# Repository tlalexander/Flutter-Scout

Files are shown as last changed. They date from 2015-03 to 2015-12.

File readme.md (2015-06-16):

# Flutter Scout printable remote control car
### Now at Version 2!

Scout is an experimental vehicle that can be printed by anyone with a 3D printer with at least 155mm of travel in one axis. The original Scout vehicles were printed on an Ultimaker, but we also recommend Printrbot, Lulzbot, and Type A Machines.

Scout does not use any screws. Sourcing screws is annoying and time consuming, and screwing things together is boring. Scout snaps together using interlocking parts and clips. The whole vehicle can be disassembled and reassembled in just a few minutes.

### Images:
http://imgur.com/a/r0YCL

### Video:
https://youtu.be/zFiCiyVp22o

### Wireless Platform
For more info on Scout's recommended wireless platform, check out http://FlutterWireless.com

### Current Issues
Scout has no crash protection for frontal crashes. Small frontal crashes can damage the steering servo horn and large direct crashes can crush the front frame member. A redesign is in the works to support a bumper and improve steering protection.
Scout V1 liked to flip over and roll back onto the wheels. Scout V2 has a flatter top and is more likely to land square upside down, requiring the operator to go flip it back over. A more turtle-like top shell should alleviate this.
Two pins in the steering system have no retaining mechanism. They will not fall out under normal operation but can fall out when Scout is upside down. This usually happens when showing someone how cool Scout's gears are.

### More details
See this blog post about Scout for some more information.
http://community.flutterwireless.com/t/introducing-flutter-scout/208

### Assembly notes

Please see the Flutter community forum for details on assembly and parts ordering for Scout.
http://community.flutterwireless.com/t/flutter-scout-robot/203

### Other notes
Flutter Scout's gears use the "Solidworks Gear Generator" file from thingiverse user msruggles, found here:
http://www.thingiverse.com/thing:8077
The developer has given me permission to use the gear files in Scout.

### License

Scout was created in early 2015 by Taylor Alexander, and is licensed under Creative Commons Attribution-ShareAlike 4.0 International (CC BY-SA 4.0), which can be viewed at: http://creativecommons.org/licenses/by-sa/4.0/

### Contact Info, press inquiries
If you would like to help with Scout or have questions for a news article, please reach out to me via email. My email is the same as my github username, but at gmail.com

### Scout V1 in the news
http://makezine.com/2015/03/12/3d-print-this-kickass-snap-together-rc-race-car/
http://blog.atmel.com/2015/03/12/scout-is-a-3d-printable-flutter-based-rc-car/

### Issues V1
These were the issues in Scout Version 1. Essentially all of them have been resolved in Version 2.

The current vehicle was designed quickly over a few weekends as a proof of concept, and so it has many flaws. A short list:
The right angle mounting of the motor creates a week point with the bevel gears.
The wheels are supposed to slip on, but using my printer they need to be hammered into place with a mallet.
The steering requires a piece of bent piano wire, and should be replaced with a printed linkage.
The body shell easily comes off, and so tape should be wrapped around the body of the system.
There is no hole in the body shell for a power switch, so without modification the tape needs to be cut to toggle power.
After agressive driving the motor gets hot and eventually wiggles in its mount.

Despite these flaws, the car is impressibly capable. It can even pull ten foot wheelies.

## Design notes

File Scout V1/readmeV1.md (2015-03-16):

# Flutter Scout printable remote control car

Scout is an experimental vehicle that can be printed by anyone with a 3D printer with at least 165mm of travel in one axis. The original Scout vehicles were printed on an Ultimaker, which is a highly recommended printer.

Scout does not use any screws. Sourcing screws is annoying and time consuming, and screwing things together is boring. Scout snaps together using interlocking parts and clips. The whole vehicle can be disassembled and reassembled in just a few minutes.

### Images:
http://imgur.com/a/Noe9S

### Video:
https://www.youtube.com/watch?v=8hfF0LrXyi8

### Scout is in the news!
http://makezine.com/2015/03/12/3d-print-this-kickass-snap-together-rc-race-car/
http://blog.atmel.com/2015/03/12/scout-is-a-3d-printable-flutter-based-rc-car/

### Wireless Platform
For more info on Scout's recommended wireless platform, check out http://www.FlutterWireless.com

### Issues

The current vehicle was designed quickly over a few weekends as a proof of concept, and so it has many flaws. A short list:
The right angle mounting of the motor creates a week point with the bevel gears.
The wheels are supposed to slip on, but using my printer they need to be hammered into place with a mallet.
The steering requires a piece of bent piano wire, and should be replaced with a printed linkage.
The body shell easily comes off, and so tape should be wrapped around the body of the system.
There is no hole in the body shell for a power switch, so without modification the tape needs to be cut to toggle power.
After agressive driving the motor gets hot and eventually wiggles in its mount.

Despite these flaws, the car is impressibly capable. It can even pull ten foot wheelies.

### Assembly notes

The wheels currently press on. If you cannot get them to fit, scale the wheel up by a few percent. If they are loose, you may want to use super glue.

The rear axle should be 100% infill for strength. Everything else can generally be 15%-30% infill (Cura calculations, other slicers may vary).

I mention using a Flutter radio to promote the product, but you can also use any normal remote control car radio, though steering may be backwards.

Any standard servo works. Other quadcopter motors should work with changes to the gear placement, but this motor is incredibly strong even with a 2s battery.

### Other notes
Flutter Scout's gears use the "Solidworks Gear Generator" file from thingiverse user msruggles, found here:
http://www.thingiverse.com/thing:8077
No license accompanies the file, but I have reached out to the developer for explicit permission. It was however shared freely on an public site so this use is assumed permitted.

### License

Scout was created in early 2015 by Taylor Alexander, and is licensed under Creative Commons Attribution-ShareAlike 4.0 International (CC BY-SA 4.0), which can be viewed at: http://creativecommons.org/licenses/by-sa/4.0/

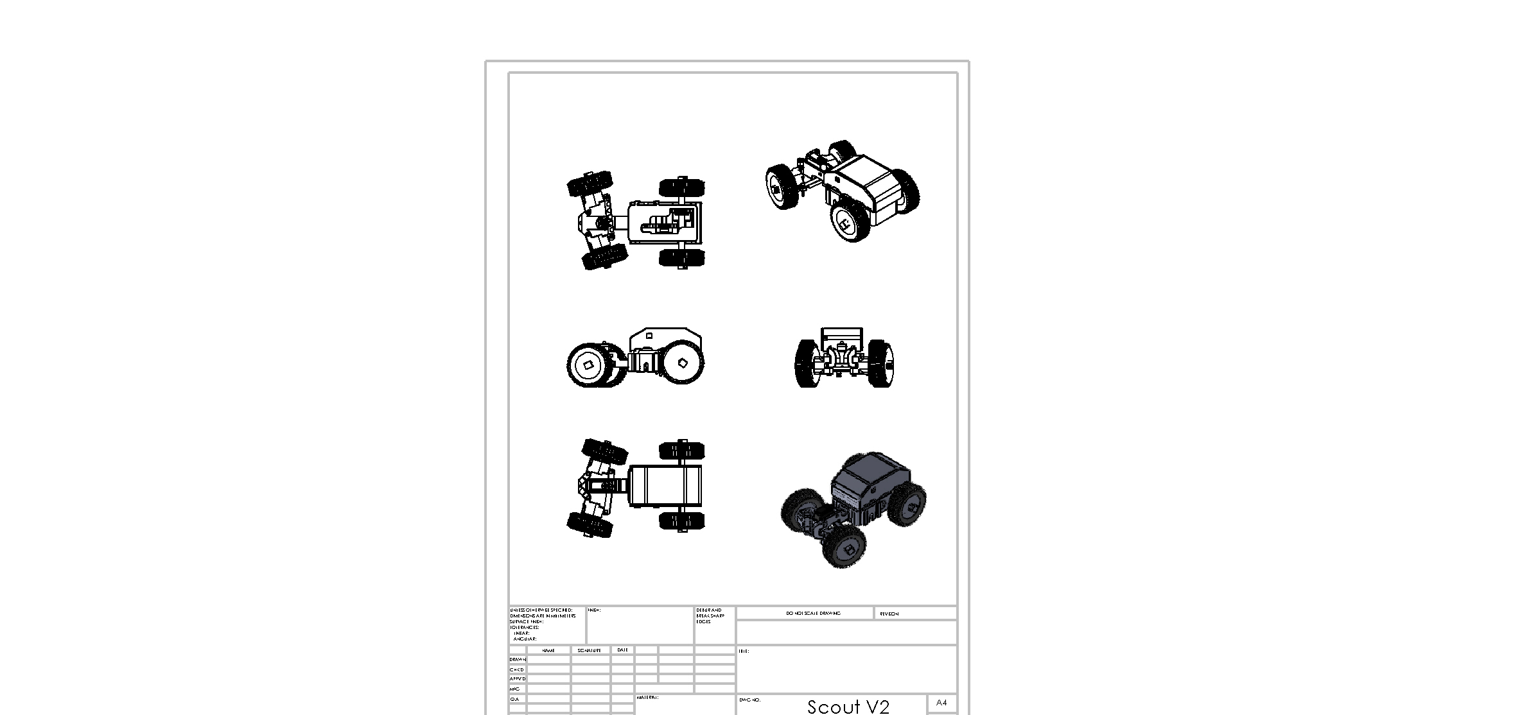
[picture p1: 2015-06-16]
Scout V2.JPG

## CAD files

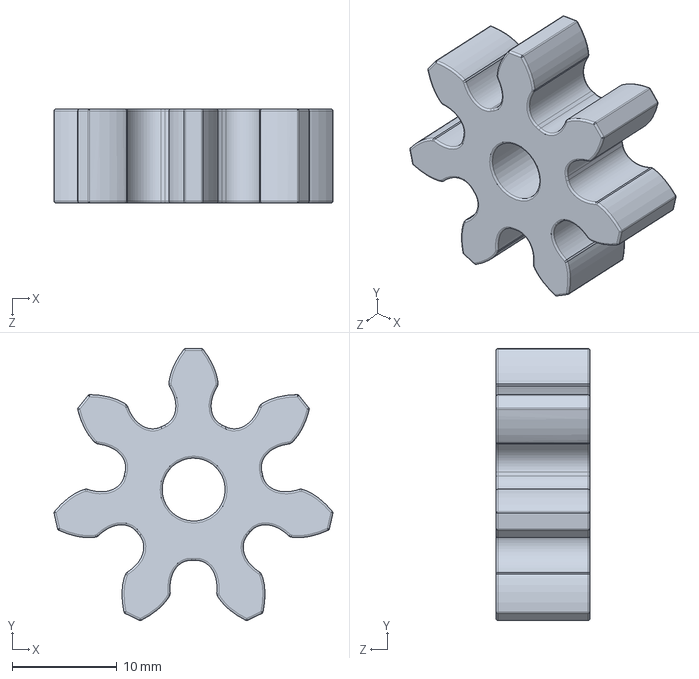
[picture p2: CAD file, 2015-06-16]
gears/main small drive gear.SLDPRT
26.6 x 26.0 x 9.00 mm

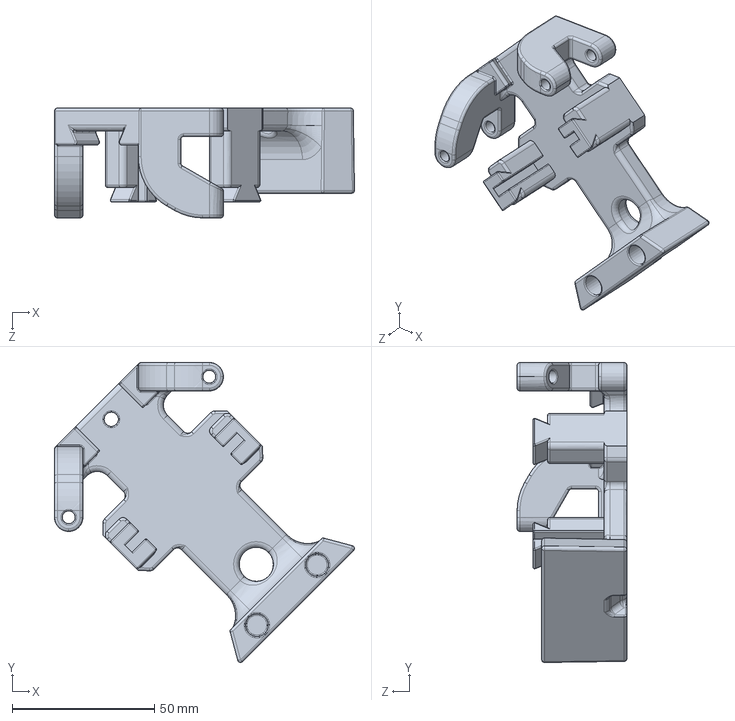
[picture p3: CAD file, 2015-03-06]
Scout V1/frame components/main frame, front.SLDPRT
105.6 x 105.6 x 38.7 mm

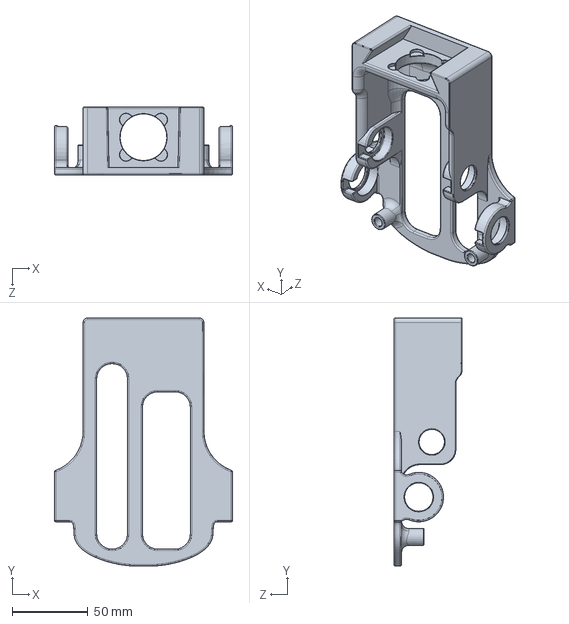
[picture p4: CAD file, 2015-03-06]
Scout V1/frame components/main frame, rear.SLDPRT
118.0 x 164.2 x 45.0 mm

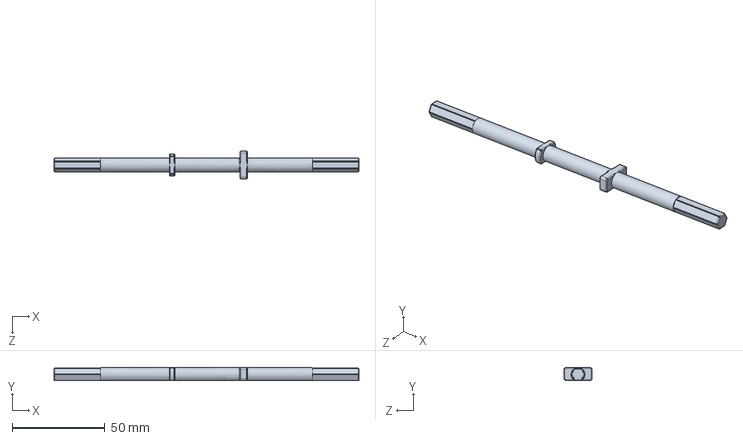
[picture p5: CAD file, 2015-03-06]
Scout V1/shafts/main axle.SLDPRT
164.0 x 7.08 x 15.0 mm

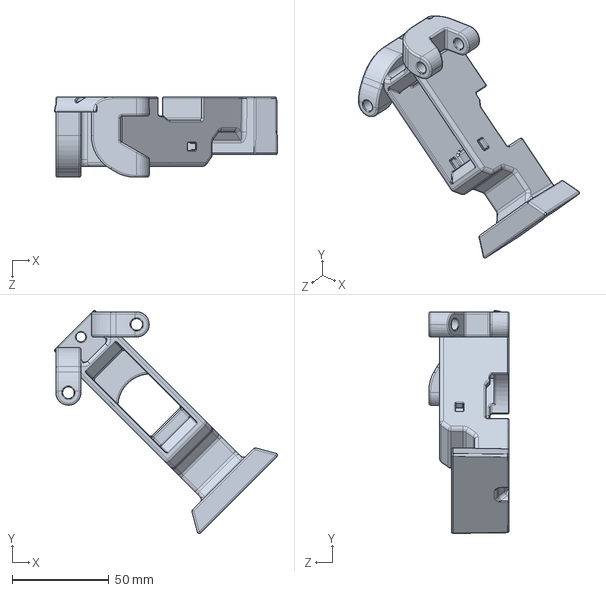
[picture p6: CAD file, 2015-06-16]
frame components/main frame, front V2.SLDPRT
115.4 x 115.4 x 41.7 mm

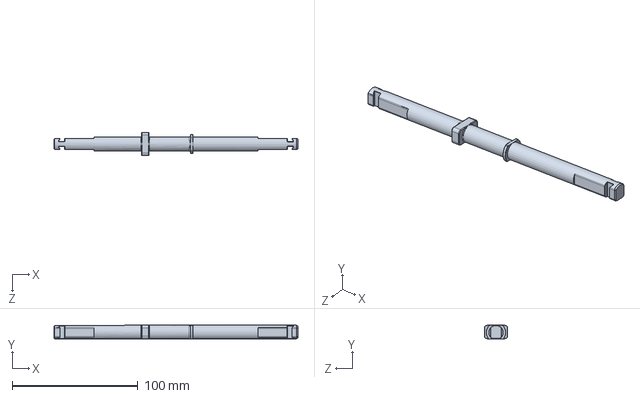
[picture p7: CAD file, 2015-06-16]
shafts/main axle 12mm.SLDPRT
194.0 x 10.8 x 18.5 mm

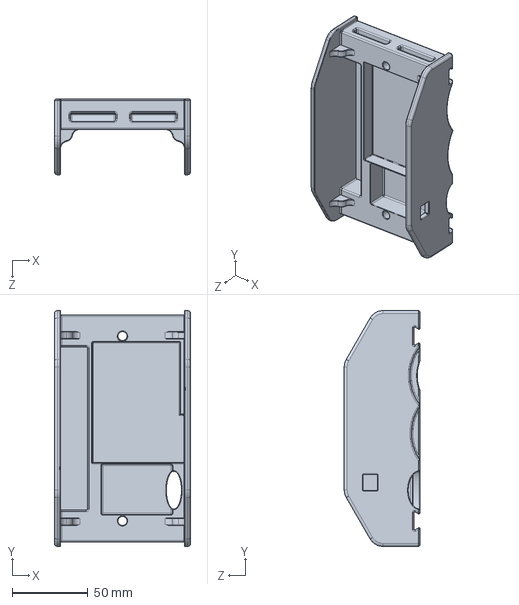
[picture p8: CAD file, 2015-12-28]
frame components/Scout tray.SLDPRT
90.0 x 156.0 x 50.0 mm

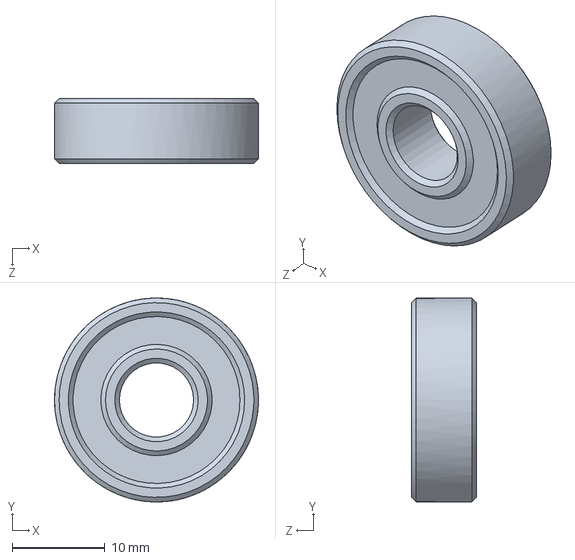
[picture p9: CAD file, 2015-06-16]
non-printed parts/608 bearing.SLDPRT
22.0 x 22.0 x 7.00 mm

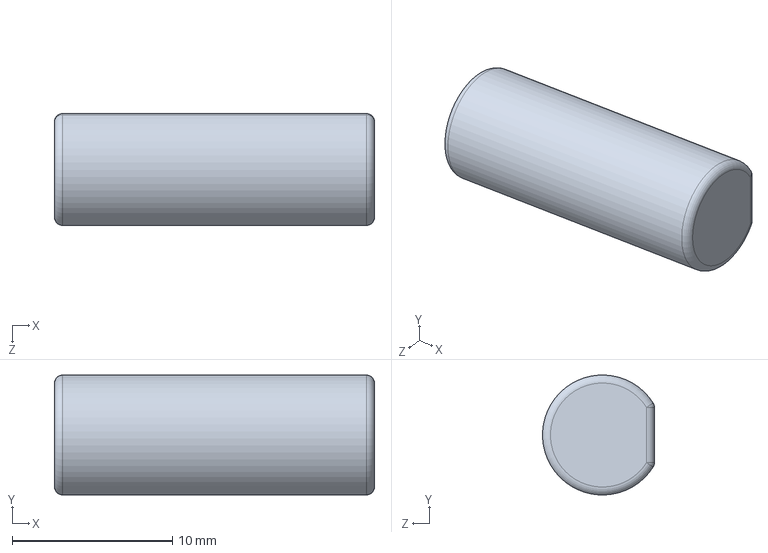
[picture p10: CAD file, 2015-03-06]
Scout V1/frame components/Body support peg front.SLDPRT
20.0 x 7.49 x 6.99 mm

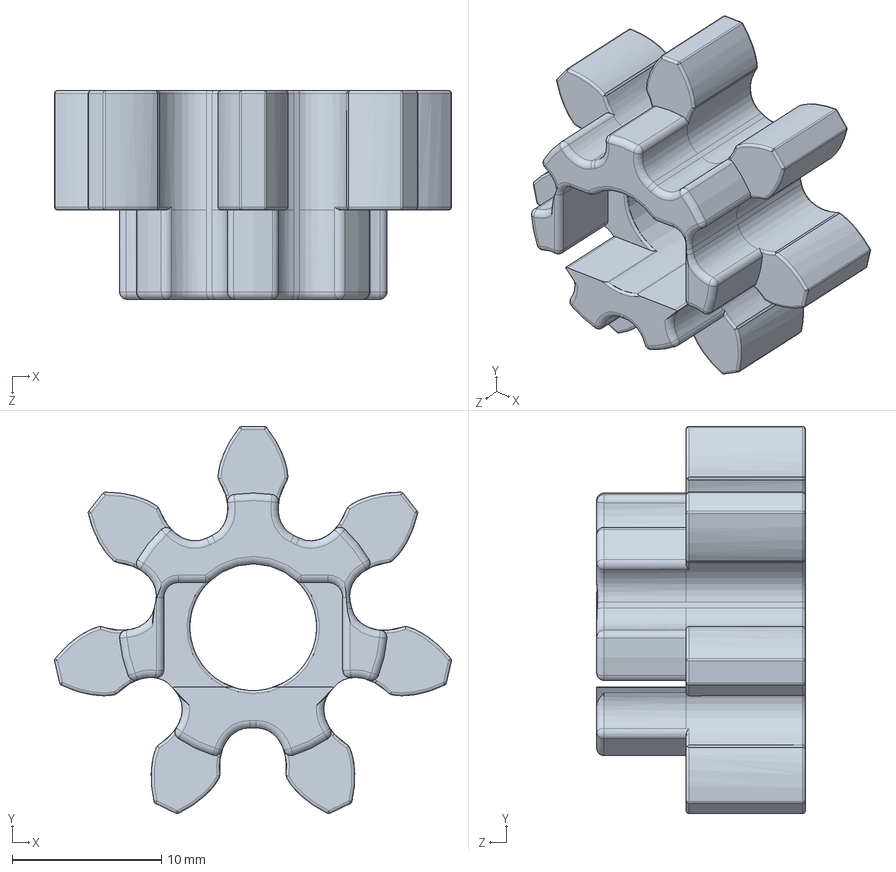
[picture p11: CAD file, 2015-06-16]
Scout V1/gears/secondary small drive gear.SLDPRT
26.6 x 26.0 x 14.0 mm

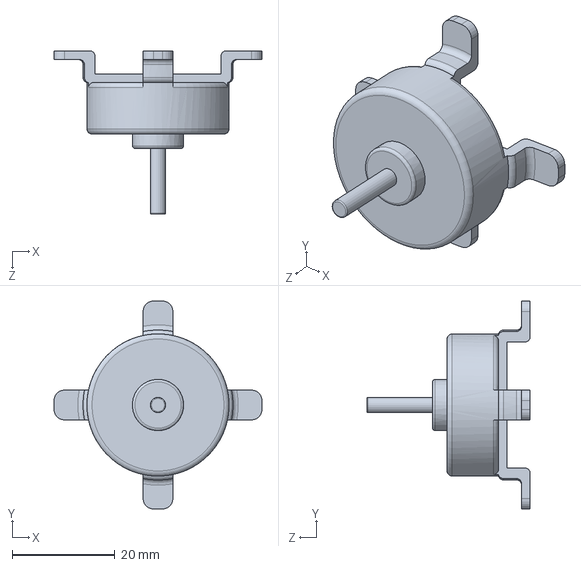
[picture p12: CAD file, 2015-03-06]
Scout V1/non-printed parts/Hobbyking Donkey ST2204.SLDPRT
40.5 x 40.5 x 31.8 mm

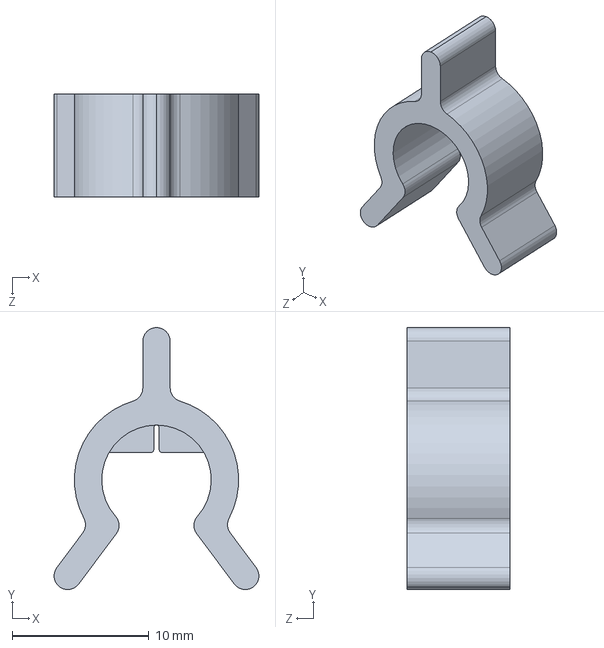
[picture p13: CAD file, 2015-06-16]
Scout V1/shafts/clip, forward drive shaft.SLDPRT
15.0 x 19.1 x 7.50 mm

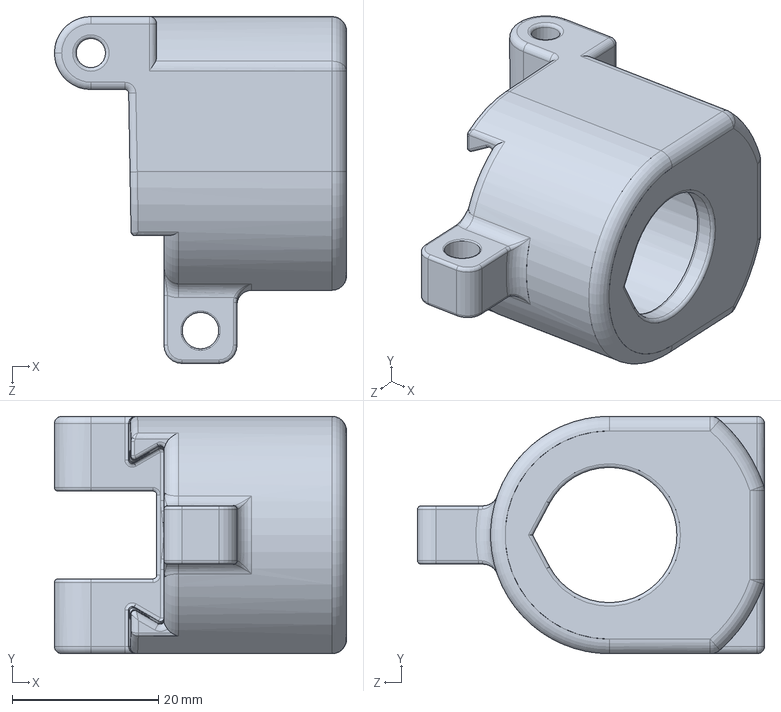
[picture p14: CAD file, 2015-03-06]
Scout V1/steering/front wheel bearing carrier.SLDPRT
40.0 x 32.5 x 47.5 mm

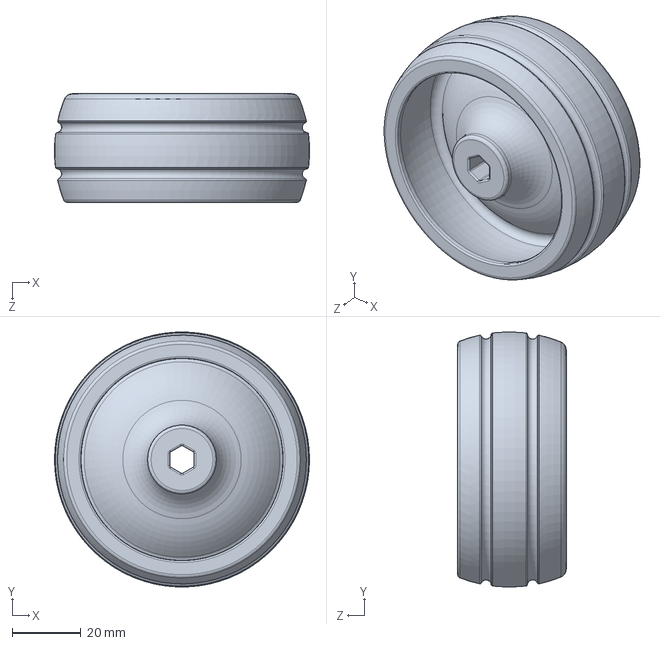
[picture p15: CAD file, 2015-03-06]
Scout V1/wheels/Rear Wheel.SLDPRT
74.1 x 74.0 x 31.6 mm

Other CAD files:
gears/small gear wrench.SLDPRT
shafts/clip 12mm, rear axle.SLDPRT
steering/front wheel bearing retainer V2.SLDPRT
wheels/Wheel Rim.SLDPRT
Scout V1/frame components/Body support peg front.STL
Scout V1/frame components/body shell tray.SLDPRT
Scout V1/frame components/body shell tray.STL
Scout V1/frame components/body shell.SLDPRT
Scout V1/frame components/body shell.STL
Scout V1/frame components/rear vertical support.SLDPRT
Scout V1/frame components/rear vertical support.STL
Scout V1/gears/bevel gear for motor.STL
Scout V1/gears/bevel gear, large.SLDPRT
Scout V1/gears/bevel gear, large.STL
Scout V1/gears/large gear for rear.SLDPRT
Scout V1/gears/secondary small drive gear.STL
Scout V1/non-printed parts/608 bearing.SLDPRT
Scout V1/non-printed parts/Turnigy TGY-S901D Servo.SLDPRT
Scout V1/shafts/clip, forward drive shaft.STL
Scout V1/shafts/clip, right rear axle.SLDPRT
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

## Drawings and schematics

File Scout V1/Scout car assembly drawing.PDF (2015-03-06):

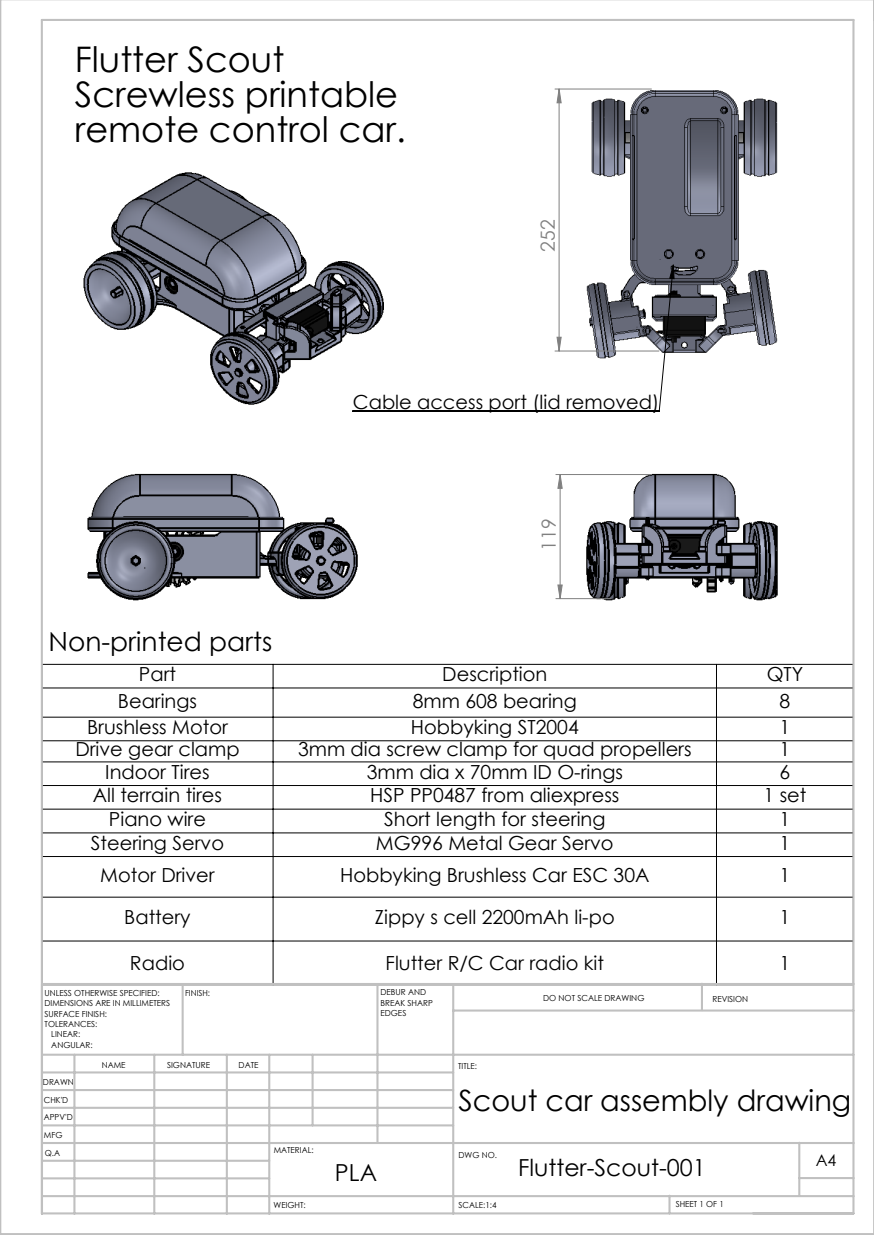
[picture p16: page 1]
SCALE:1:4; SHEET 1 OF 1

Flutter Scout
Screwless printable
remote control car.

Cable access port (lid removed) 119

Non-printed parts

Part | Description | QTY
Bearings | 8mm 608 bearing | 8
Brushless Motor | Hobbyking ST2004 | 1
Drive gear clamp | 3mm dia screw clamp for quad propellers | 1
Indoor Tires | 3mm dia x 70mm ID O-rings | 6
All terrain tires | HSP PP0487 from aliexpress | 1 set
Piano wire | Short length for steering | 1
Steering Servo | MG996 Metal Gear Servo | 1
Motor Driver | Hobbyking Brushless Car ESC 30A | 1
Battery | Zippy s cell 2200mAh li-po | 1
Radio | Flutter R/C Car radio kit | 1

UNLESS OTHERWISE SPECIFIED: DIMENSIONS ARE IN MILLIMETERS SURFACE FINISH: TOLERANCES: LINEAR: ANGULAR: | FINISH: | DEBUR AND BREAK SHARP EDGES | DO NOT SCALE DRAWING | REVISION
NAME | SIGNATURE | DATE | | | | TITLE: Scout car assembly drawing

DRAWN
CHK'D
APPV'D
MFG
Q.A | | | | MATERIAL: PLA | DWG NO. Flutter-Scout-001 | A4

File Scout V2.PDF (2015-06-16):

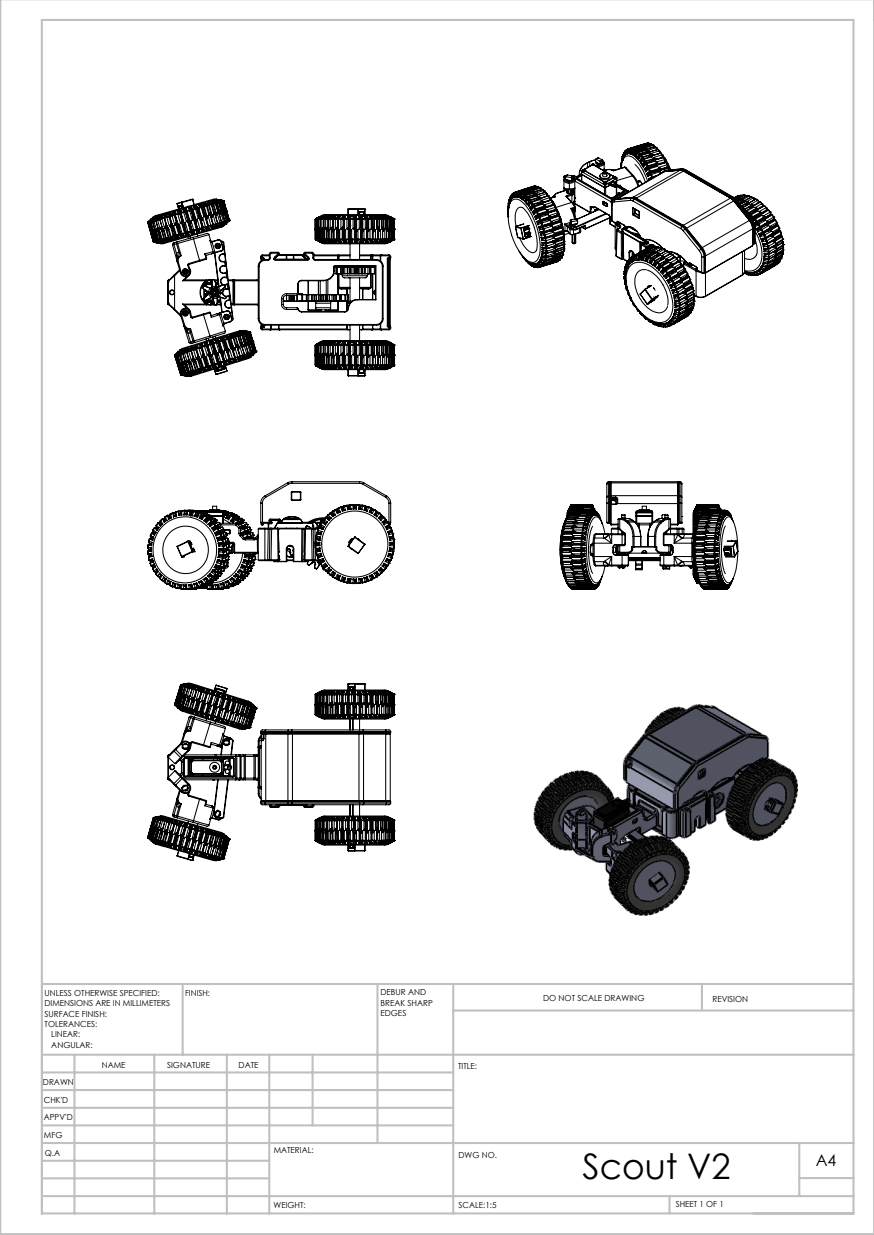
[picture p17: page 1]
SCALE:1:5; SHEET 1 OF 1; DO NOT SCALE DRAWING; REVISION; DEBUR AND BREAK SHARP; UNLESS OTHERWISE SPECIFIED:; FINISH:

DIMENSIONS ARE IN MILLIMETERS
SURFACE FINISH:
TOLERANCES:
LINEAR:
ANGULAR:

NAME | SIGNATURE | DATE | | | | TITLE:
Q.A | | | | MATERIAL: | Scout V2 WEIGHT: DWG NO. | A4

DRAWN
CHK'D
APPV'D
MFG

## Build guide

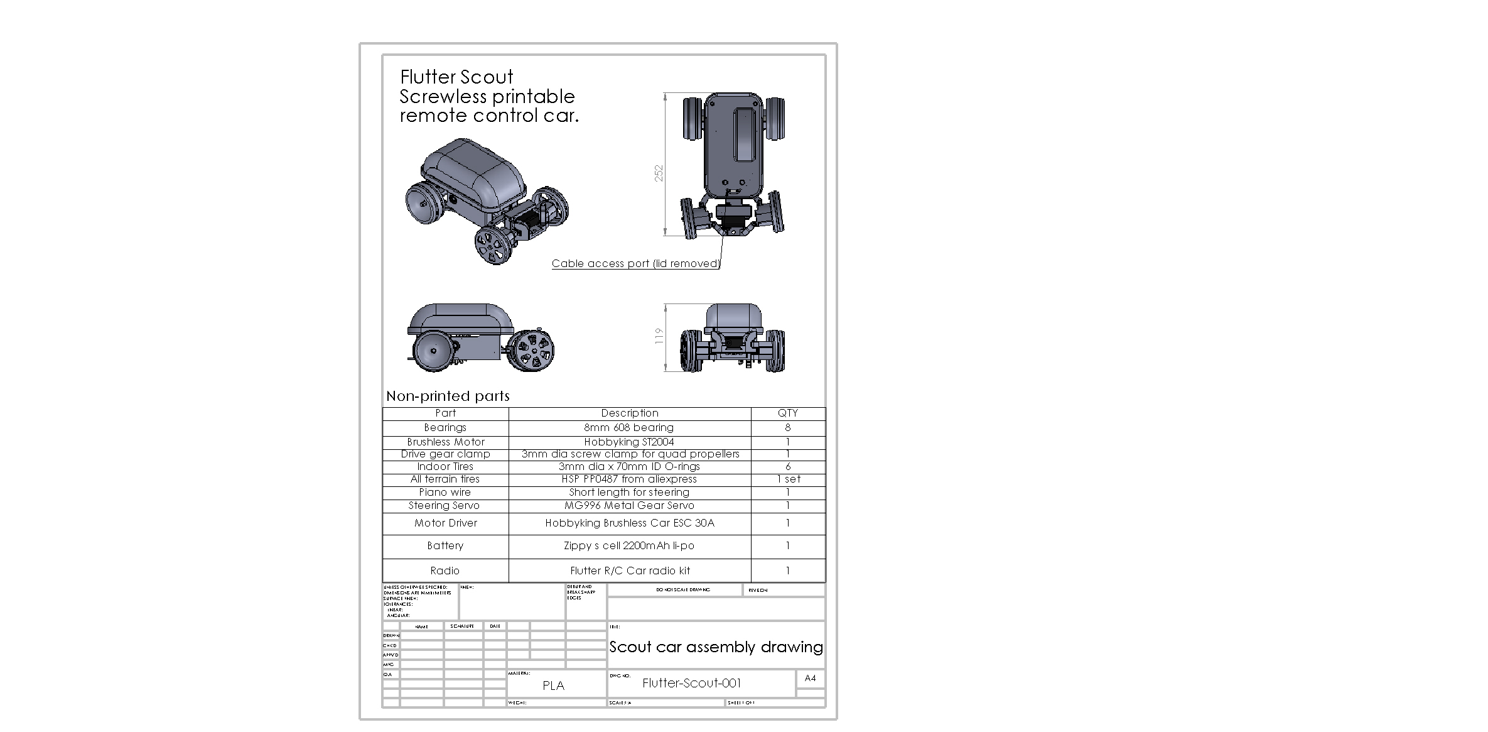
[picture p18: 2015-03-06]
Scout V1/Scout car assembly drawing.JPG

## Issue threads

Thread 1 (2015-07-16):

STL missing for secondary small drive gear

garyjohnson, 2015-07-16:
Noticed the STL is missing for the secondary small drive gear. Unfortunately Solidworks is out of my reach, so I can't do it myself. : )

Also it would be great to see if there was an export path to get from the parametric SLDPRT files into something that was editable in a free / cheap tool like 123D Design or Fusion 360 so the community could contribute and fork. Not sure how realistic that is without a full rebuild in a separate program.

vinceallenvince, 2015-07-18:
I used the one in the V1 folder. I haven't finished printing the Scout and don't know if this is the correct version. But it may be worth a shot if you are further along than me.
https://github.com/tlalexander/Flutter-Scout/blob/master/Scout%20V1/gears/secondary%20small%20drive%20gear.STL

tlalexander, 2015-12-28:
Added it where it should be with d18c20cd94da170de3f17c1c40a759d41630a3ed.
Thanks!

Closed 2015-12-28.

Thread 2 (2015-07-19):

missing 12mm shaft clip

vinceallenvince, 2015-07-19:
I can't find the 12 mm shaft clip described in step K of the Make magazine article. I'm guessing it's version 2 of the clip-left-rear-axle found in the V1 shafts folder. However, this clip is too small.

https://github.com/tlalexander/Flutter-Scout/blob/master/Scout%20V1/shafts/clip.%20left%20rear%20axle.STL

tlalexander, 2015-12-28:
Fixed with d18c20cd94da170de3f17c1c40a759d41630a3ed.
Thanks!

Closed 2015-12-28.

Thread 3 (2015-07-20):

Simple wrench for holding propeller gear not included

drubaby, 2015-07-20:
Can't seem to find the file for the simple 3D printed wrench referenced in step L of the make zine article.

tlalexander, 2015-12-28:
Added with d18c20cd94da170de3f17c1c40a759d41630a3ed.
Thanks!

Closed 2015-12-28.

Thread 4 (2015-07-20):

8mm shaft clip file missing

drubaby, 2015-07-20:
Can't seem to find the file for the "8mm shaft clip" referenced in step i of the make zine article.

tlalexander, 2015-12-28:
Fixed with d18c20cd94da170de3f17c1c40a759d41630a3ed
Thanks!

Closed 2015-12-28.

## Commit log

2015-03-06 Flutter Scout, initial commit
    [608 bearing.SLDPRT, Body support peg front.SLDPRT, Body support peg front.STL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]
2015-03-12 fixed Flutter wireless URL in readme
2015-03-16 Updated readme to point to gear file source.
2015-06-16 Initial commit of Scout V2 files.
    [12mm shaft end clip.SLDPRT, 12mm shaft end clip.STL, 12mm shaft.SLDPRT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]
2015-06-16 Added complete vehicle drawing, with PDF and JPG. And added contact info to readme.
    [front wheel bearing retainer V2.SLDPRT]
2015-12-28 Added source and STL for 12mm shaft clip, 8mm shaft clip, and gear wrench. Also added STL for secondary drive gear.
    [Scout tray.SLDPRT, clip 12mm, rear axle.SLDPRT, clip 12mm, rear axle.STL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]
